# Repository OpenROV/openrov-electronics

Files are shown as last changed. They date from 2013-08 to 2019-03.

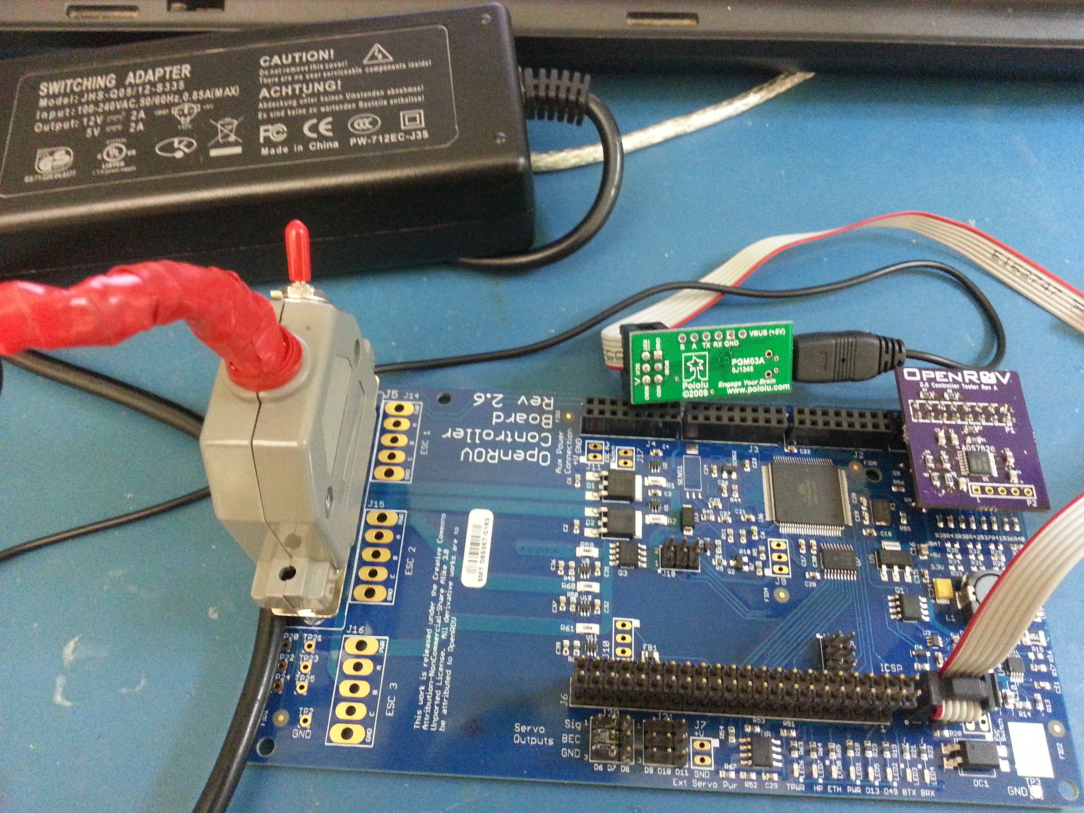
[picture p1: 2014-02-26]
OpenROV Controller Tester 2.6A/TestJig_Setup.jpg

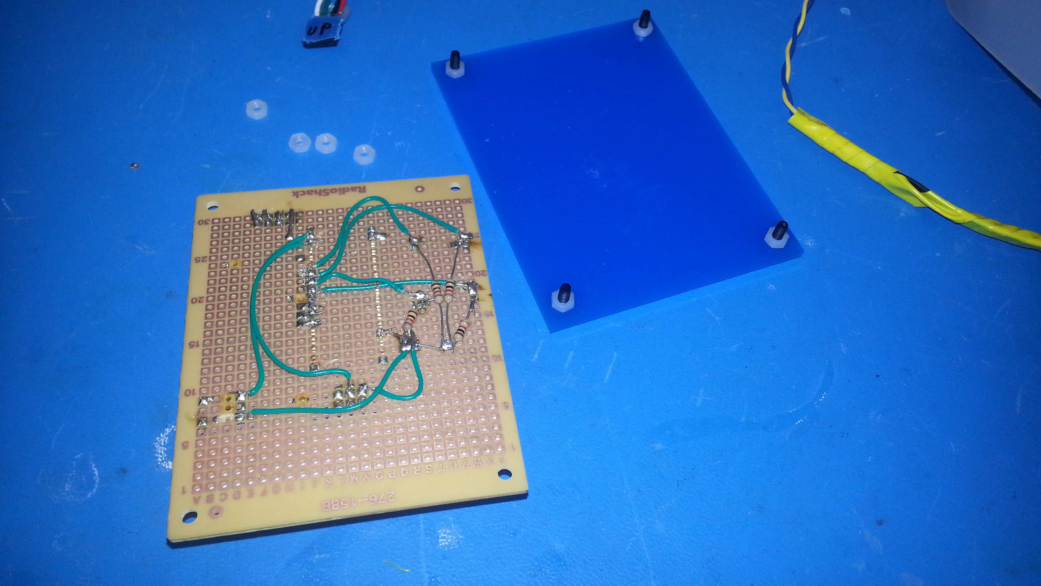
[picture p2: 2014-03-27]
OpenROV IMU Tester/backside2.jpg

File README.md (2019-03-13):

OpenROV
================
[OpenROV](http://openrov.com/) is a DIY telerobotics community centered around underwater exploration & adventure. Our [forum](https://forum.openrov.com/) is the primary place for community interaction and we encourage you to join us there!

Introduction
-------
This repository contains the electronics files for the OpenROV DIY Kits. These include the schematics, gerbers and the other files + diagrams.

Resources
-------
[Bill of Materials](https://docs.google.com/spreadsheet/ccc?key=0Avf6fUwp9B3kdF9YQWxBTnZjZEVGZVQwY25EbnVyREE&usp=sharing)

[Mechanical files](https://github.com/OpenROV/openrov-hardware)

Notes
-------
For OpenROV v2.6, v2.7, v2.8 see the OpenROV Controller Board Files.
  >It is a all-in-one power and control board that has an Arduino based Atmega 2560 aboard. Tons of I/O, and is designed to fit the BeagleBone Black.

For OpenROV v2.5 See the OpenROV Controller 2.5B. 
  >It is a all-in-one power and control board that has an Arduino based Atmega 2560 aboard. Tons of I/O, and is designed to fit both the BeagleBone Black and the original BeagleBone

For OpenROV V2.3 and V2.4, see the BeagleBone Cape A1. 
  >It is a all-in one power and control board based around the Atmega 328.

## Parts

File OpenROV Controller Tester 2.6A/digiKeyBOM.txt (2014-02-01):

Index,Quantity,Part Number,Description,Customer Reference,Available Quantity,Backorder Quantity,Unit Price USD,Extended Price USD,
1,3,296-12402-1-ND,IC ADC 12BIT 50KSPS 8CH 16TSSOP,,3,0,8.94000,$26.82,
2,10,399-1170-1-ND,CAP CER 0.1UF 50V 10% X7R 0805,,10,0,0.04400,$0.44,
3,5,399-1284-1-ND,CAP CER 1UF 16V 10% X7R 0805,,5,0,0.12000,$0.60,
4,20,RMCF0805FT10K0CT-ND,RES 10K OHM 1/8W 1% 0805,,20,0,0.02900,$0.58,
5,10,RMCF0805FT20K0CT-ND,RES 20K OHM 1/8W 1% 0805,,10,0,0.02900,$0.29,
6,10,311-49.9KCRCT-ND,RES 49.9K OHM 1/8W 1% 0805 SMD,,10,0,0.01900,$0.19,
7,12,RMCF0805JT4K70CT-ND,RES 4.7K OHM 1/8W 5% 0805,,12,0,0.02100,$0.25,
,,,,,,Subtotal,$29.17
,,,,,,Shipping,unknown
,,,,,,Estimated Sales Tax,$2.63
,,,,,,Total,unknown

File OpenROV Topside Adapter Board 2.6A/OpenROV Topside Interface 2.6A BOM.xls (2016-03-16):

 |  |  |  | OpenROV Topside Adapter 2.6A BOM - 11 Feb 2014
Parts | Qty | DNP? | OK to sub Sonic part? | Digi-Key Part# | Value | Device | Package | Description
C1, C2 | 2 |  | X | 1276-1082-1-ND | 10 uF X7R 16V | CAP1206 | R1206 | Generic Non-Polarized Capacitor
FB1 | 1 |  |  | 240-2551-1-ND | MI0805J102R-10 | FERRITESIZE_0805 | R0805 | Generic Surface Mount Ferrite Chip
FID1, FID2 | 2 | X |  |  | FIDUCIAL_1 | FIDUCIAL_1 | FIDUCIAL_1 | Alignment Fiducial
J1 | 1 |  | X | 609-4701-1-ND | FCI 10033526-N3212MLF | USB_MINI-BSURFACE_MOUNT | USB_MINI-B_SM | MINI USB-B Conector
J2 | 1 |  |  | 609-4537-ND | FCI 20020303-D021 | FCI_TERMINAL_BLOCK_2PL | FCI_09-381_2PL | FCI 2-place Terminal Block 09-381 / 20020303
J3, J4 | 2 |  | X | S2211EC-03-ND | Sullins PRPC003DFAN-RC | Header Pins 2x3 | SSW-103-02-S-D | 2X3 THROUGH-HOLE .025" SQ PINS w/ 0.32" Engagement Length
J5 | 1 | X |  |  |  | HDR_1X2X0.100-ALT_SILK | 22-23-2021_ALT_SILK | .100" (2.54mm) Center Header - 2 Pin
LED1 | 1 |  |  | 475-1404-1-ND | GREEN | LED-0805_BOTTOM_MT | LED_0805_BOTTOM_MT(OSRAM) | Generic LED
LED2, LED3 | 2 |  |  | 475-2553-1-ND | YELLOW | LED-0805_BOTTOM_MT | LED_0805_BOTTOM_MT(OSRAM) | Generic LED
R1 | 1 |  | X |  | 1K | RESISTOR-0805 | R0805 | Generic Resistor
R2, R6 | 2 |  | X |  | 0 (Jumper) | RESISTOR-0805 | R0805 | Generic Resistor
R3, R4 | 2 |  | X |  | 120 | RESISTOR-0805 | R0805 | Generic Resistor
R5 | 1 |  | X |  | 330 | RESISTOR-0805 | R0805 | Generic Resistor
U1 | 1 |  |  | AP1117IE33G-13DICT-ND | AP1117IE33G | AP1117SOT223 | SOT223 | Diodes, Inc. Voltage Regulator

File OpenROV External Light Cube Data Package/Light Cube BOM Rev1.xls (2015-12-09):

 |  |  |  | OpenROV Light Cube BOM - Revision 1 --- 8 Oct 2015
Qty | DNP? | OK to sub Sonic Part? | Digi-Key Part # | Value | Device | Package | Parts | Description
1 |  | X |  | 10 uF X6S 35V | CAP0805 | R0805 | C1 | Generic Non-Polarized Capacitor
1 |  | X |  | 1.0uF X7R 16V | CAP0603 | R0603 | C2 | Generic Non-Polarized Capacitor
2 |  |  | 568-4128-1-ND | PMEG3015EJ | SCHOTTKYSOD323 | SOD323 | D1, D3 | Silicon Schottky Diodes
1 |  |  | LM4040DIX3-2.5+TCT-ND | LM4040DIX3-2.5 | ZENER-TVS-SC70-3 | SC70-3 | D2 | Generic Zener Diode, TVS, or Reference Diode
1 |  |  | 240-2558-1-ND | MI0603L221R-10 | FERRITESIZE_0603 | R0603 | FB1 | Generic Surface Mount Ferrite Chip
1 | DNP |  |  |  | SMD_PAD3/3 | SMD_3_3 | GND | SMD PAD
1 |  |  | 240-2743-1-ND | 33 uH | INDUCTOR-LAIRD_TYS6045 | INDUCTOR_LAIRD_TYS6045 | L1 | Generic Inductor Footprint
1 |  |  | Mouser 941-XHP50A10D0BJ20E5 | CREE XHP50 4000K 1040 lm | LED_WITH_HEATSINK-CREE_XHP50_6V | CREE_XHP50_6V | LED1 | Power LED packages with a heatsink pad
1 |  |  | SI2318CDS-T1-GE3CT-ND | Si2318CDS | NMOS-FETSOT23 | SOT23 | Q1 | Generic NMOS FET
1 |  |  | 541-4.99KYCT-ND | 4.99K 1% 1/8W | RESISTOR-0402 | R0402 | R1 | Generic Resistor
1 |  |  | 490-6992-1-ND | Murata PRF18BG471QB5RB | RESISTOR-0603 | R0603 | R2 | Generic Resistor
2 |  | X |  | 4.7K 1% | RESISTOR-0402 | R0402 | R3, R5 | Generic Resistor
1 |  |  | 408-1421-1-ND | 0.12 1% 1/5W or higher | RESISTOR-0603 | R0603 | R4 | Generic Resistor
1 |  |  | ILD 4001 E6327CT-ND | ILD4001 | ILD4001 | SC74_INFINEON | U1 | Infineon ILD4001 Buck LED Controller
1 | DNP |  |  |  | SMD_PAD-2/2 | SMD_2_2 | V+ | SMD PAD

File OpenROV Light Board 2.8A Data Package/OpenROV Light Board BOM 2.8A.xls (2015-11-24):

 |  |  | OpenROV Light Board 2.8A BOM - 23 November 2015
Qty | DNP? | OK to sub Sonic Part? | Digi-Key Part # | Value | Device | Package | Parts | Description
3 |  | X |  | 0.01 uF X7R 50V | CAP0603 | R0603 | C1, C2, C4 | Generic Non-Polarized Capacitor
1 |  | X |  | 1A 30V Schottky | SCHOTTKYDO214AC | DO214AC | D1 | Silicon Schottky Diodes
1 |  |  | 507-1817-1-ND | 80mA /200 mA 15V | POLYFUSE-0603 | R0603 | F1 | Polyfuse / PPTC
2 | DNP |  |  | FIDUCIAL_1 | FIDUCIAL_1 | FIDUCIAL_1 | FID1, FID2 | Alignment Fiducial
2 | DNP |  |  |  | SOLDER_PADS_3MM | SOLDER_PADS_3MM | J1, J2 | Custom 3mm solder pads for OROV light board
2 | DNP |  |  |  | SOLDER_PADS_3MM-SMALL_HOLE | SOLDER_PADS_3MM_SMALL_HOLE | J3, J4 | Custom 3mm solder pads for OROV light board
4 |  |  | 160-2093-1-ND | LTW-5630AZL35 | LTW-5630AZL | LITEON-5630 | LED1, LED2, LED3, LED4 | Lite-On 5x3 mm LTW-5630AZL White LED
3 |  | X |  | 4.99K 1% | RESISTOR-0603 | R0603 | R1, R2, R3 | Generic Resistor
1 | DNP |  |  | DNP | RESISTOR-1206 | R1206 | R4 | Generic Resistor
2 |  |  | AL5812MP-13DICT-ND | AL5812MP-13 | AL5812MP-13 | MSOP-8EP | U1, U2 | Diodes, Inc AL5812 LED Driver

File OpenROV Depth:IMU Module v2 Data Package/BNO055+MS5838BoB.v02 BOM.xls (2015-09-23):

 |  |  | OpenROV Depth/IMU V2 BOM - 20 May 2015
Qty | DNP? | OK to sub Sonic part? | Part # | Value | Device | Package | Parts | Description
3 |  | X |  | 100 nF X5R 6.3V or greater | C-EUC0402 | C0402 | C1, C2, C3 | CAPACITOR, European symbol
1 |  | X |  | 6800 pF X7R 6.3V or greater | C-EUC0402 | C0402 | C4 | CAPACITOR, European symbol
1 |  | X |  | 4.7 uF X5R 6.3V or greater | C-EUC0402 | C0402 | C5 | CAPACITOR, European symbol
1 |  | X |  | 0.12 uF X5R 6.3V or greater | C-EUC0402 | C0402 | C6 | CAPACITOR, European symbol
2 | DNP |  |  | FIDUCIALUFIDUCIAL | FIDUCIALUFIDUCIAL | MICRO-FIDUCIAL | FID1, FID2 | Fiducial Alignment Points
2 | DNP |  |  | M021X02_NO_SILK | M021X02_NO_SILK | 1X02_NO_SILK | JP2, JP3 | Standard 2-pin 0.1" header. Use with
4 |  | X |  | 4K7 | R-US_R0402 | R0402 | R1, R2, R3, R5 | RESISTOR, American symbol
1 |  |  | Mouser 262-BNO055 | Bosch BNO055 | BN055 | LGA28 | U1
1 |  |  | MS5837-30BA | MS5837-30BA | MS5837 | MS5837 | U2 | Measurement Specialties' MS5837 Depth Sensor

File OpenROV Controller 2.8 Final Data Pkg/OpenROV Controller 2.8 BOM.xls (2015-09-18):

 |  |  | OpenROV Controller 2.8 BOM - 27 May 2015
Qty | DNP? | OK to sub Sonic Part? | Digi-Key Part # | Value | Device | Package | Parts | Description
25 |  | X |  | 0.1 uF | CAP0603 | R0603 | C1, C2, C3, C4, C5, C6, C7, C12, C15, C17, C18, C21, C22, C23, C24, C25, C26, C27, C28, C29, C30, C31, C32, C33, C43 | Generic Non-Polarized Capacitor
2 |  | X |  | 3900 pF 25V NP0 | CAP0603 | R0603 | C10, C11 | Generic Non-Polarized Capacitor
2 |  | X |  | 22 uF 10V X5R | CAP0805 | R0805 | C13, C14 | Generic Non-Polarized Capacitor
2 |  | X |  | 12 pF | CAP0603 | R0603 | C19, C20 | Generic Non-Polarized Capacitor
1 |  |  | 493-2098-1-ND | 220 uF 10V | CAP-POLARIZED-NICHICON-8MM | NICHICON_8MM | C34 | Electrolytic or Tantalum Capacitor
9 |  | X |  | 1 uF 25V X7R | CAP0603 | R0603 | C36, C37, C38, C42, C44, C45, C46, C47, C48 | Generic Non-Polarized Capacitor
3 |  |  | 493-3958-1-ND | 220 uF 35V Low-Impedance | CAP-POLARIZED-NICHICON-10MM | NICHICON_10MM | C39, C40, C41 | Electrolytic or Tantalum Capacitor
4 |  | X |  | 10 uF 25V X5R | CAP0805 | R0805 | C8, C9, C16, C35 | Generic Non-Polarized Capacitor
2 |  |  | MBRD835LT4GOSCT-ND | MBRD835L | SCHOTTKYDPAK | DPAK | D1, D2 | Silicon Schottky Diodes
1 |  |  | SMAJ18ALFCT-ND | SMAJ18A | ZENER-TVSDO-214AC | DO214AC | D3 | Generic Zener Diode, TVS, or Reference Diode
2 |  |  | MM3Z16VST1GOSCT-ND | 16.18V 2% | ZENER-TVSSOD323 | SOD323 | D4, D5 | Generic Zener Diode, TVS, or Reference Diode
1 |  |  | SMAJ15ALFCT-ND | SMAJ15A | ZENER-TVSDO-214AC | DO214AC | D6 | Generic Zener Diode, TVS, or Reference Diode
4 |  |  | S1AFSCT-ND | S1A | DIODE | DO214AC | D7, D8, D9, D10 | Generic Diode Devices
1 |  |  | 507-1749-1-ND | 2.0A / 4.0A 24V | POLYFUSE-2920 | R2920 | F1 | Polyfuse / PPTC
1 |  |  | 240-2504-1-ND | HZ0805B272R-10 | FERRITESIZE_0805 | R0805 | FB1 | Generic Surface Mount Ferrite Chip
5 | DNP |  |  | FIDUCIAL_1 | FIDUCIAL_1 | FIDUCIAL_1 | FID1, FID2, FID3, FID4, FID5 | Alignment Fiducial
1 |  | X | S7111-ND | Sullins PPPC082LFBN-RC | HDR_SOCKET_2X8 | SSW-108-02-S-D | J1 | 2x8 THROUGH-HOLE .025" SQ POST SOCKET
1 |  | X | SAM1030-03-ND |  | HDR_PINS_2X3 | HDR_PINS_2X3 | J13 | 2x3 PIN HEADER
1 |  |  |  | AfroESC 12A-stuff per instructions | ESC_PADS-AFRO-12/20A-ESC1S | AFRO-ESC-12/20A-ESC1S | J14 | Solder Pads for Various ESC Types
1 |  |  |  | AfroESC 12A-stuff per instructions | ESC_PADS-AFRO-12/20A-ESC2S | AFRO-ESC-12/20A-ESC2S | J15 | Solder Pads for Various ESC Types
1 |  |  |  | AfroESC 12A-stuff per instructions | ESC_PADS-AFRO-12/20A-ESC3S | AFRO-ESC-12/20A-ESC3S | J16 | Solder Pads for Various ESC Types
2 |  | X | S2211EC-03-ND | Sullins PRPC003DFAN-RC | HDR_SOCKET_2X3 | SSW-103-02-S-D | J18, J19 | 2X3 THROUGH-HOLE .025" SQ POST SOCKET
3 | DNP |  |  | PPPC082LFBN-RC (Not populated) | HDR_SOCKET_2X8 | SSW-108-02-S-D | J2, J3, J4 | 2x8 THROUGH-HOLE .025" SQ POST SOCKET
2 |  | X |  | TSW-103-07-G-T | HDR_PINS_3X3 | HDR_PINS_3X3 | J20, J21 | 3x3 0.100 Header Pins
1 |  |  | 182-25ME-ND | Norcomp 182-025-113R531 | M25VP | M25VP | J5 | 25-pin Vertical Male D-SUB
1 |  | X | Samtec DW-23-11-G-D-630 | Samtec DW-23-11-G-D-630 | BEAGLEBONE_PIN_HEADER | TSW-123-02-S-D | J6 | 46-pin Header for BeagleBone
4 | DNP |  |  |  | HDR_1X2X0.100-ALT_SILK | 22-23-2021_ALT_SILK | J7, J11, J12, J17 | .100" (2.54mm) Center Header - 2 Pin
2 | DNP |  |  |  | HDR_1X3X0.100-ALT_SILK | 22-23-2031_ALT_SILK | J9, J10 | .100" (2.54mm) Center Header - 3 Pin
1 |  |  | SRR1260-150MCT-ND | 15 uH 4A | INDUCTOR-BOURNS-12X0 | INDUCTOR_BOURNS_12X0 | L1 | Generic Inductor Footprint
2 |  |  | 475-2709-1-ND | GREEN | LED-0603 | LED_CHIPLED_0603 | LED1, LED6 | Generic LED
2 |  |  | 475-2506-1-ND | RED | LED-0603 | LED_CHIPLED_0603 | LED2, LED5 | Generic LED
4 |  |  | 475-1196-1-ND | YELLOW | LED-0603 | LED_CHIPLED_0603 | LED3, LED4, LED7, LED8 | Generic LED
1 |  |  | 160-2035-1-ND | LTV-8141S | LTV-8141S | DIL4-SMD | OC1 | Lite-On Bidirectional-Input Optocoupler
1 |  |  | 425-2103-1-ND | PC3H411NIP0F | OPTOCOUPLER-TRANSISTOR-BIDIR-MINIFLAT-HALFPITCH | OPTOCOUPLER-MINIFLAT-HALFPITCH | OC2 | Optocoupler with Bidirectional Input and Phototransistor Output (no Base Lead)
1 |  |  | SI4485DY-T1-GE3CT-ND | SI4485 | PMOS-FET | SO8 | Q1 | Generic PMOS FET
1 |  |  | DMN65D8L-7DICT-ND | DMN65D8L | NMOS-FETSOT23 | SOT23 | Q2 | Generic NMOS FET
1 |  |  | SI4459ADY-T1-GE3CT-ND | SI4459ADY | PMOS-FET | SO8 | Q3 | Generic PMOS FET
4 |  |  | IRLML6346TRPBFCT-ND | IRLML6346TR | NMOS-FETSOT23 | SOT23 | Q4, Q5, Q6, Q7 | Generic NMOS FET
2 |  |  | FDV301NCT-ND | FDV301N | NMOS-FETSOT23 | SOT23 | Q8, Q9 | Generic NMOS FET
5 |  |  | MCS1632R005FERCT-ND | 0.005 1% | RESISTOR-1206 | R1206 | R1, R2, R59, R60, R61 | Generic Resistor
2 |  | X |  | 10.0K 1% | RESISTOR-0603 | R0603 | R11, R17 | Generic Resistor
1 |  |  | WSLB-.025CT-ND | 0.025 1% | RESISTOR-0805 | R0805 | R12 | Generic Resistor
2 |  | X |  | 100K | RESISTOR-0603 | R0603 | R13, R20 | Generic Resistor
1 |  | X |  | 13.0K 1% | RESISTOR-0603 | R0603 | R14 | Generic Resistor
1 |  | X |  | 45.3K 1% | RESISTOR-0603 | R0603 | R16 | Generic Resistor
1 |  | X |  | 470 | RESISTOR-0603 | R0603 | R21 | Generic Resistor
9 | DNP |  |  | DNP | RESISTOR-0805 | R0805 | R24, R25, R27, R29, R30, R31, R33, R34, R35 | Generic Resistor
8 |  | X |  | 0 (Jumper) | RESISTOR-0805 | R0805 | R26, R28, R32, R70, R71, R72, R73, R74 | Generic Resistor
1 |  | X |  | 18K | RESISTOR-0603 | R0603 | R3 | Generic Resistor
3 |  | X |  | 30.1K 1% | RESISTOR-0603 | R0603 | R4, R10, R76 | Generic Resistor
1 | DNP |  |  | DNP | RESISTOR-0603 | R0603 | R47 | Generic Resistor
1 |  | X |  | 0 (Jumper) | RESISTOR-0603 | R0603 | R48 | Generic Resistor
6 |  | X |  | 3.3K | RESISTOR-0603 | R0603 | R49, R50, R66, R67, R68, R69 | Generic Resistor
12 |  | X |  | 1K | RESISTOR-0603 | R0603 | R5, R8, R9, R18, R19, R22, R23, R36, R37, R38, R39, R46 | Generic Resistor
8 |  | X |  | 4.7K | RESISTOR-0603 | R0603 | R51, R52, R53, R54, R55, R56, R57, R58 | Generic Resistor
11 |  | X |  | 10K | RESISTOR-0603 | R0603 | R6, R7, R15, R40, R41, R42, R43, R44, R45, R62, R75 | Generic Resistor
2 |  | X |  | 120 | RESISTOR-0603 | R0603 | R63, R64 | Generic Resistor
1 |  | X |  | 330 | RESISTOR-0603 | R0603 | R65 | Generic Resistor
1 | DNP |  |  | HIH-5031 (Not populated) | HIH-5031 | HIH-5031 | SENS1 | Honeywell Humidity Sensor
1 |  |  | MCP9701AT-E/TTCT-ND | MCP9701A | MCP9701 | SOT23 | SENS2 | Microchip Temperature Sensor. "A" version has better accuracy
9 | DNP |  |  |  | TEST_PAD-1.0 | 2.0/1.0 | TP1, TP2, TP3, TP20, TP21, TP22, TP23, TP24, TP25 | THROUGH-HOLE PADS
6 |  |  | 296-27331-1-ND | INA199A2 | INA199 | SC70-6L | U1, U2, U3, U9, U10, U11
1 |  |  | TCR2EF33LM(CTCT-ND | TCR2EF33 | TCR2EF | SOT23-5L | U12 | Toshiba TCR2EF 200 mA LDO Regulator
1 |  |  | 1028-1002-1-ND | Richtek RT8250 | RICHTEK_82XX | SO8-THERMAL | U4 | Richtek 82XX-series synchronous buck converter in SO-8 package
1 |  |  | 296-35976-1-ND | TLV1117LV33DCY | AP1117SOT223 | SOT223 | U5 | Diodes, Inc. Voltage Regulator
1 |  |  | ATMEGA2560-16AURCT-ND | ATMEGA2560-16AU | SMARTPRJ_ATMEGA25602560-16AU | SMARTPRJ_TQFP100 | U6 | ATMEGA MICROCONTROLLER from Arduino Refernce Design
1 |  |  | 296-21527-1-ND | TXB0108SSOP-20 | TXB0108SSOP-20 | SSOP-20 | U7 | TI Bidirectional Level Translator
1 |  |  | CAT24C256WI-GT3OSCT-ND | CAT24C256WI-G | CAT24C256WI-G | SO8 | U8 | I2C EEPROM for BeagleBone Capes
1 |  |  | 887-1747-1-ND | 16 MHz w/ 12pF Load | CRYSTAL-5*3.2 | DISCRETE_2P-SMD-5X3.2 | X1 | Crystal

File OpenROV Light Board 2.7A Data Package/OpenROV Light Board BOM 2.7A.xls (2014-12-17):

 |  |  | OpenROV Light Board 2.7A BOM - 7 September 2014
Qty | DNP? | OK to sub Sonic Part? | Digi-Key Part # | Value | Device | Package | Parts | Description
3 |  | X |  | 0.01 uF X7R 50V | CAP0603 | R0603 | C1, C2, C4 | Generic Non-Polarized Capacitor
1 |  | X |  | 1A 30V Schottky | SCHOTTKYDO214AC | DO214AC | D1 | Silicon Schottky Diodes
1 |  |  | 507-1817-1-ND | 80mA /120 mA 15V | POLYFUSE-0603 | R0603 | F1 | Polyfuse / PPTC
2 | DNP |  |  | FIDUCIAL_1 | FIDUCIAL_1 | FIDUCIAL_1 | FID1, FID2 | Alignment Fiducial
2 | DNP |  |  |  | HDR_1X2X0.100-ALT_SILK | 22-23-2021_ALT_SILK | J1, J2 | .100" (2.54mm) Center Header - 2 Pin
2 | DNP |  |  |  | HDR_1X2X2MM | 87758-0216 | J3, J4 | Original Source: Eagle Lib con-molex/87758-0216
4 |  |  | 160-2093-1-ND | LTW-5630AZL35 | LTW-5630AZL | LITEON-5630 | LED1, LED2, LED3, LED4 | Lite-On 5x3 mm LTW-5630AZL White LED
3 |  | X |  | 4.99K 1% | RESISTOR-0603 | R0603 | R1, R2, R3 | Generic Resistor
1 | DNP |  |  | DNP | RESISTOR-1206 | R1206 | R4 | Generic Resistor
2 |  |  | AL5812MP-13DICT-ND | AL5812MP-13 | AL5812MP-13 | MSOP-8EP | U1, U2 | Diodes, Inc AL5812 LED Driver

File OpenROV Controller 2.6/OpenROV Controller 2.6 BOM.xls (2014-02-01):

 |  |  | OpenROV Controller 2.6 BOM -- 13 Nov 2013
Qty | DNP? | OK to sub Sonic Part | Digi-Key Part# | Value | Device | Package | Parts | Description
27 |  | X | 445-1314-1-ND | 0.1 uF 50V X7R | CAP0603 | R0603 | C1, C2, C3, C4, C5, C6, C7, C12, C15, C17, C18, C21, C22, C23, C24, C25, C26, C27, C28, C29, C30, C31, C32, C33, C36, C37, C38 | Generic Non-Polarized Capacitor
1 |  | X | 399-1083-1-ND | 1000 pF 50V X7R | CAP0603 | R0603 | C11 | Generic Non-Polarized Capacitor
3 |  | X | 445-7660-1-ND | 10 uF 10V X5R | CAP0805 | R0805 | C13, C14, C16 | Generic Non-Polarized Capacitor
2 |  | X | 445-1270-1-ND | 12 pF NPO | CAP0603 | R0603 | C19, C20 | Generic Non-Polarized Capacitor
1 |  | X | 399-5756-1-ND | 220 uF 6.3V | CAP-POLARIZED-B_CASE | KEMET_B-CAPACITOR | C34
1 | DNP |  |  | DNP | CAP0805 | R0805 | C35 | Generic Non-Polarized Capacitor
3 |  | X | 1276-2396-1-ND | 1 uF 50V X5R | CAP0805 | R0805 | C8, C9, C10 | Generic Non-Polarized Capacitor
2 |  |  | MBRD835LT4GOSCT-ND | MBRD835L | SCHOTTKYDPAK | DPAK | D1, D2 | Silicon Schottky Diodes
1 |  |  | SMAJ22ALFCT-ND | SMAJ22A | ZENER-TVSDO-214AC | DO214AC | D3 | Generic Zener Diode or TVS
2 |  |  | MM3Z16VST1GOSCT-ND | 16.18V 2% | ZENER-TVSSOD323 | SOD323 | D4, D5 | Generic Zener Diode or TVS
1 |  |  | 641-1101-1-ND | CDBA340 | SCHOTTKYDO214AC | DO214AC | D6 | Silicon Schottky Diodes
4 |  |  | S1AFSCT-ND | S1A | DIODE | DO214AC | D7, D8, D9, D10 | Generic Diode Devices
1 |  |  | F5632CT-ND | 1.95A / 1.1A | POLYFUSE-1812 | R1812 | F1 | Polyfuse / PPTC
1 |  |  | 240-2504-1-ND | HZ0805B272R-10 | FERRITESIZE_0805 | R0805 | FB1 | Generic Surface Mount Ferrite Chip
5 | DNP |  |  | FIDUCIAL_1 | FIDUCIAL_1 | FIDUCIAL_1 | FID1, FID2, FID3, FID4, FID5 | Alignment Fiducial
4 |  | X | S7111-ND | Sullins PPPC082LFBN-RC | HDR_SOCKET_2X8 | SSW-108-02-S-D | J1, J2, J3, J4 | 2x8 THROUGH-HOLE .025" SQ POST SOCKET
1 |  | X | SAM1030-03-ND | Samtec TSW-103-07-L-D | HDR_PINS_2X3 | HDR_PINS_2X3 | J13 | 2x3 PIN HEADER
3 | DNP |  |  |  | ESC_PADS-0.156_ALT | ESC-PADS-.156-ALT_SILK | J14, J15, J16 | Solder Pads for ESC
2 |  | X | SAM1208-03-ND | SSW-103-01-G-D | HDR_SOCKET_2X3 | SSW-103-02-S-D | J18, J19 | 2X3 THROUGH-HOLE .025" SQ POST SOCKET
2 |  | X |  | TSW-103-07-G-T | HDR_PINS_3X3 | HDR_PINS_3X3 | J20, J21 | 3x3 0.100 Header Pins
1 |  |  | 609-3993-ND | FCI 10090096-P254 | M25VP | M25VP | J5 | 25-pin Vertical Male D-SUB
1 |  | X | Samtec DW-23-11-G-D-630 | Samtec DW-23-11-G-D-630 | BEAGLEBONE_PIN_HEADER | TSW-123-02-S-D | J6 | 46-pin Header for BeagleBone
4 | DNP |  |  |  | HDR_1X2X0.100-ALT_SILK | 22-23-2021_ALT_SILK | J7, J11, J12, J17 | .100" (2.54mm) Center Header - 2 Pin
2 | DNP |  |  |  | HDR_1X3X0.100-ALT_SILK | 22-23-2031_ALT_SILK | J9, J10 | .100" (2.54mm) Center Header - 3 Pin
1 |  |  | Order from Coilcraft | MSS1048-153MLB | INDUCTOR-MSS1048 | MSS1048 | L1 | Coilcraft MSS1048-series inductors
2 |  |  | 475-2709-1-ND | GREEN | LED-0603 | LED_CHIPLED_0603 | LED1, LED6 | Generic LED
2 |  |  | 475-2506-1-ND | RED | LED-0603 | LED_CHIPLED_0603 | LED2, LED5 | Generic LED
4 |  |  | 475-1196-1-ND | YELLOW | LED-0603 | LED_CHIPLED_0603 | LED3, LED4, LED7, LED8 | Generic LED
1 |  |  | 160-2035-1-ND | LTV-8141S | LTV-8141S | DIL4-SMD | OC1 | Lite-On Bidirectional-Input Optocoupler
1 |  |  | SI4485DY-T1-GE3CT-ND | SI4485 | PMOS-FET | SO8 | Q1 | Generic PMOS FET
1 |  |  | DMN65D8L-7DICT-ND | DMN65D8L | NMOS-FETSOT23 | SOT23 | Q2 | Generic NMOS FET
1 |  |  | SI4425DDY-T1-GE3CT-ND | SI4425 | PMOS-FET | SO8 | Q3 | Generic PMOS FET
4 |  |  | IRLML6346TRPBFCT-ND | IRLML6346TR | NMOS-FETSOT23 | SOT23 | Q4, Q5, Q6, Q7 | Generic NMOS FET
2 |  |  | FDV301NCT-ND | FDV301N | NMOS-FETSOT23 | SOT23 | Q8, Q9 | Generic NMOS FET
5 |  |  | MCS1632R005FERCT-ND | 0.005 1% | RESISTOR-1206 | R1206 | R1, R2, R59, R60, R61 | Generic Resistor
1 |  | X | P30.1KHCT-ND | 30.1K 1% | RESISTOR-0603 | R0603 | R10 | Generic Resistor
2 |  | X | P10.0KHCT-ND | 10.0K 1% | RESISTOR-0603 | R0603 | R11, R17 | Generic Resistor
1 |  |  | WSLB-.025CT-ND | 0.025 1% | RESISTOR-0805 | R0805 | R12 | Generic Resistor
1 |  | X | P133KHCT-ND | 133K 1% | RESISTOR-0603 | R0603 | R14 | Generic Resistor
1 |  |  | P75NACT-ND | 0.075 1% | RESISTOR-1210 | R1210 | R15 | Generic Resistor
1 |  | X | P9.76KHCT-ND | 9.76K 1% | RESISTOR-0603 | R0603 | R16 | Generic Resistor
1 |  | X | P100KGCT-ND | 100K | RESISTOR-0603 | R0603 | R20 | Generic Resistor
1 |  | X | P470GCT-ND | 470 | RESISTOR-0603 | R0603 | R21 | Generic Resistor
11 | DNP |  |  | DNP | RESISTOR-0603 | R0603 | R24, R25, R27, R29, R30, R31, R32, R33, R34, R35, R47 | Generic Resistor
4 |  | X | P0.0GCT-ND | 0 (Jumper) | RESISTOR-0603 | R0603 | R26, R28, R48, R67 | Generic Resistor
1 |  | X | P18KGCT-ND | 18K | RESISTOR-0603 | R0603 | R3 | Generic Resistor
14 |  | X | P10KGCT-ND | 10K | RESISTOR-0603 | R0603 | R4, R6, R7, R13, R40, R41, R42, R43, R44, R45, R49, R50, R62, R66 | Generic Resistor
12 |  | X | P1.0KGCT-ND | 1K | RESISTOR-0603 | R0603 | R5, R8, R9, R18, R19, R22, R23, R36, R37, R38, R39, R46 | Generic Resistor
8 |  | X | P4.7KGCT-ND | 4.7K | RESISTOR-0603 | R0603 | R51, R52, R53, R54, R55, R56, R57, R58 | Generic Resistor
2 |  | X | P120GCT-ND | 120 | RESISTOR-0603 | R0603 | R63, R64 | Generic Resistor
1 |  | X | P330GCT-ND | 330 | RESISTOR-0603 | R0603 | R65 | Generic Resistor
1 | DNP |  |  | HIH-5031 | HIH-5031 | HIH-5031 | SENS1 | Honeywell Humidity Sensor
1 |  |  | MCP9701AT-E/TTCT-ND | MCP9701A | MCP9701 | SOT23 | SENS2 | Microchip Temperature Sensor. "A" version has better accuracy
8 | DNP |  |  |  | TEST_PAD-1.0 | 2.0/1.0 | TP2, TP3, TP20, TP21, TP22, TP23, TP24, TP25 | THROUGH-HOLE PADS
6 |  |  | 296-27331-1-ND | INA199A2 | INA199 | SC70-6L | U1, U2, U3, U9, U10, U11
1 |  |  | LM25011MY/NOPBCT-ND | LM25011 | LM25011 | VSSOP-10 | U4 | TI LM25011 Switching Converter
1 |  |  | 296-35976-1-ND | TLV1117LV33 | AP1117SOT223 | SOT223 | U5 | Diodes, Inc. Voltage Regulator
1 |  |  | ATMEGA2560-16AURCT-ND | ATMEGA2560-16AU | SMARTPRJ_ATMEGA25602560-16AU | SMARTPRJ_TQFP100 | U6 | ATMEGA MICROCONTROLLER from Arduino Refernce Design
1 |  |  | 296-21527-1-ND | TXB0108SSOP-20 | TXB0108SSOP-20 | SSOP-20 | U7 | TI Bidirectional Level Translator
1 |  |  | CAT24C256WI-GT3OSCT-ND | CAT24C256WI-G | CAT24C256WI-G | SO8 | U8 | I2C EEPROM for BeagleBone Capes
1 |  |  | 887-1747-1-ND | 16 MHz w/ 12 pF load | CRYSTAL-5*3.2 | DISCRETE_2P-SMD-5X3.2 | X1 | Crystal

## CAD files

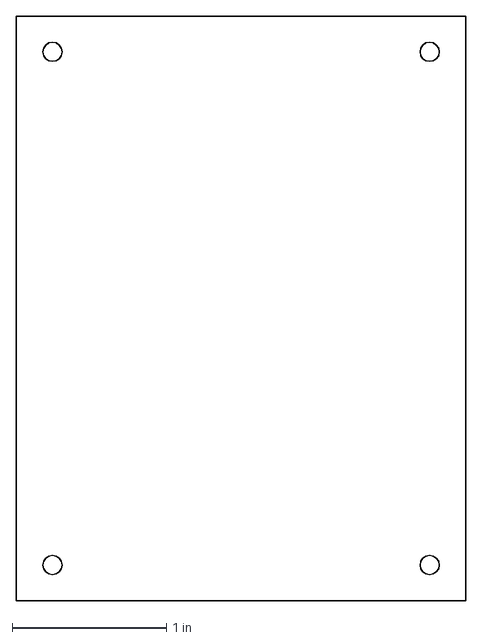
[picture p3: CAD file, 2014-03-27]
OpenROV IMU Tester/IMUTesterBottom.dxf
2.91 x 3.79 in

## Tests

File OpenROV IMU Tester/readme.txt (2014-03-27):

OpenROV IMU tester by Matthew Valancy! 

Basic bare IMU board test

1) Plug in the tester to USB power.
2) Connect IMU by tilting board on the header
3) Press soft reset button (the black one) 
4) Look at lights to see if IMU is OK
5) If IMU light is red then switch the address switch on the bottom of the tester and it will retest

Testing on ROV
Same as above but use Brians cable (DB25 to 4 pin IMU header)

Want to build another one because the original got destroyed or lost?

You need 4 LEDS, 1 toggle switch, 1 push button switch, 1 arduino. 
Wire with LEDS connected to ground through 1k resistor with positive side on arduino.
Toggle switch and push button are pulled high by arduino and set low when active.
Pins are shown in the arduino code.

Good luck.

Need help? scubasonar@gmail.com

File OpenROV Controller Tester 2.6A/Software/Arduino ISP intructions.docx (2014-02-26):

30 Oct 2013 W. Holm

Instructions for using the Pololu AVR ISP programmer with the Arduino IDE to program the OpenROV 2.5 boards

1.) Go to the Pololu web site, download the drivers for the programmer, and install them on your computer.

2.) Download the Arduino IDE and install. I'm using version 1.0.5.

3. Go to the directory C:\Program Files (x86)\Arduino\hardware\arduino

4.) Append the following text to the bottom of the programmers.txt file:

avrispv2.name=Pololu USB (AVRISPv2)

avrispv2.communication=serial

avrispv2.protocol=avrispv2

5.) Append the following text to the bottom of the boards.txt file:

mega2560p.name=Arduino Mega 2560 with Pololu AVR ISP

#mega2560p.upload.protocol=wiring

mega2560p.upload.using=avrispv2

mega2560p.upload.maximum_size=258048

#mega2560p.upload.speed=115200

mega2560.bootloader.low_fuses=0xFF

mega2560.bootloader.high_fuses=0xD8

mega2560.bootloader.extended_fuses=0xFD

mega2560.bootloader.path=stk500v2

mega2560.bootloader.file=stk500boot_v2_mega2560.hex

mega2560.bootloader.unlock_bits=0x3F

mega2560.bootloader.lock_bits=0x0F

mega2560p.build.mcu=atmega2560

mega2560p.build.f_cpu=16000000L

mega2560p.build.core=arduino

mega2560p.build.variant=mega

6.) Plug in the Pololu programmer to your computer.

7.) Probe what serial port is assigned to the programmer

8.) Open the Arduino IDE.

9.) In Tools/Boards, select "Arduino Mega 2560 with Pololu AVR ISP"

*we’ve been using Arduino Mega 2560 or Mega ADK

10.) In Tools/Programmer, select "Pololu USB"

11.) In Tools/Serial Port, select the serial port that the Pololu programmer is attached to.

12.) Apply power to the OROV controller board. The Pololu ISP cable does not apply power to the target.

13.) Attach the Pololu ISP cable to the ISP port on the board.

14.) Select Tools/Burn Bootloader and wait for the bootloader to be downloaded into the Controller board.

15.) Upload your desired sketch as you normally would in the Arduino IDE. Note that the serial monitor in the IDE will not work.

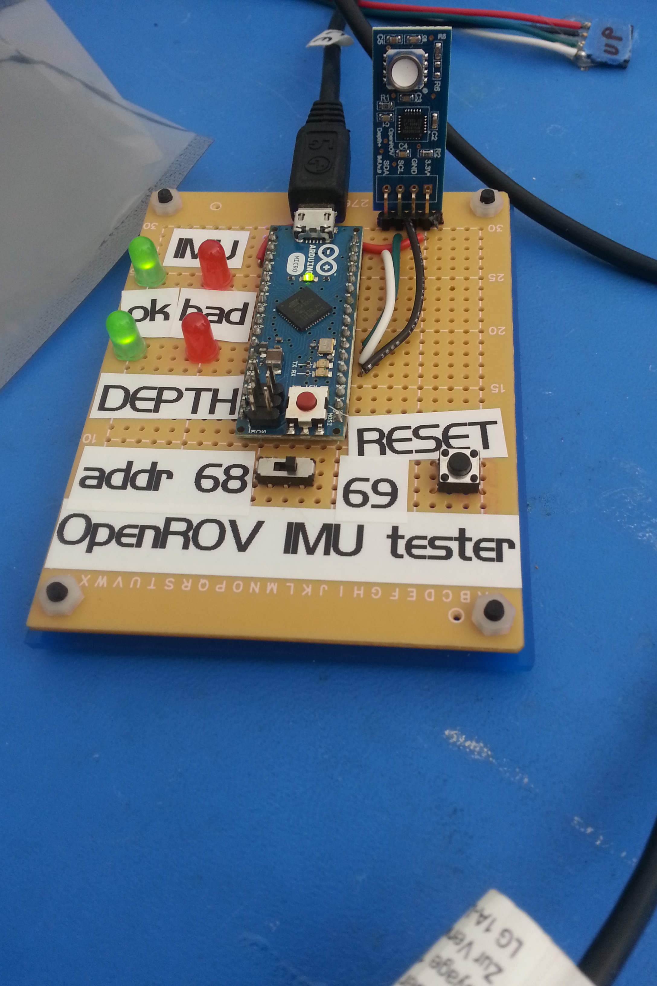
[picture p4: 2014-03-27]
OpenROV IMU Tester/front.jpg

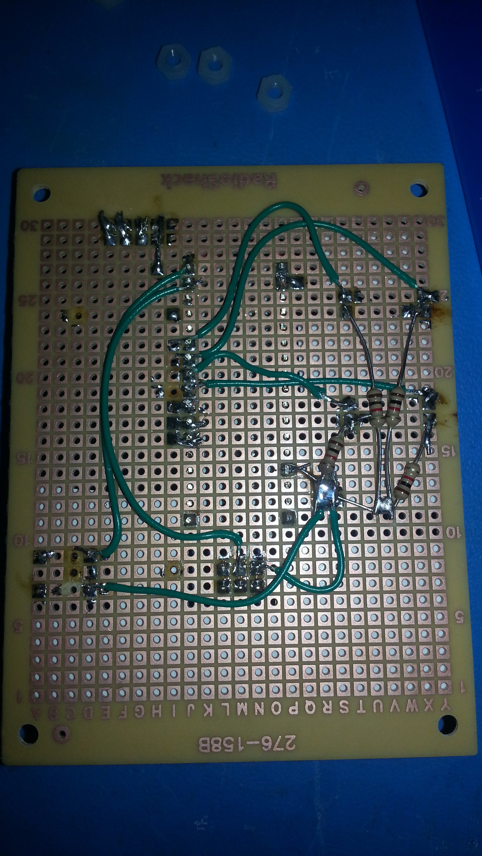
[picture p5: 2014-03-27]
OpenROV IMU Tester/backside.jpg

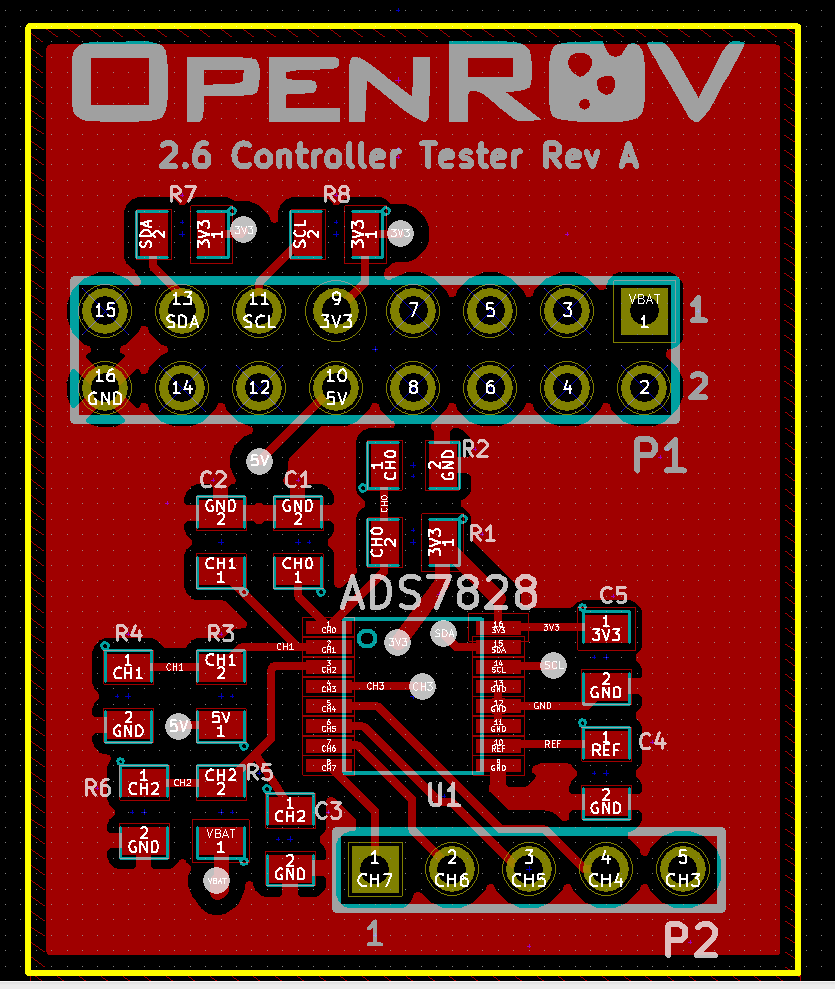
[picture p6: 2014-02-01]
OpenROV Controller Tester 2.6A/Controller Tester 2.6A Layout.png

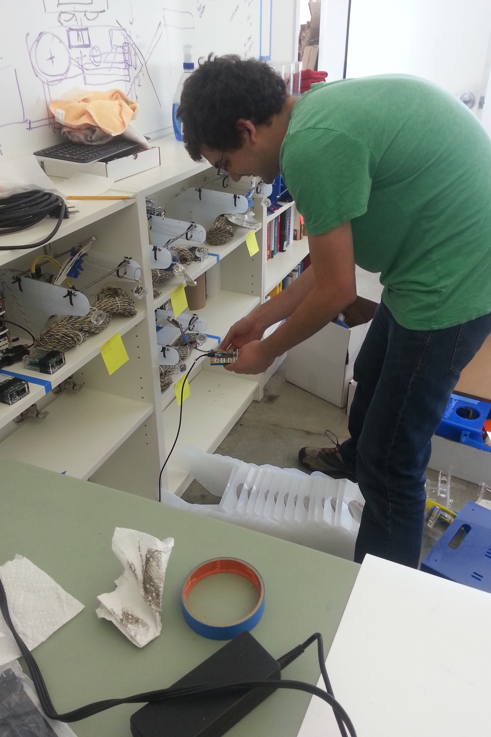
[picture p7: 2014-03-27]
OpenROV IMU Tester/inUse.jpg

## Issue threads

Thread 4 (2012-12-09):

No Clearance for Aux 2 Connector

davidtlang, 2012-12-09:
There isn't enough clearance for the Aux 2 connector because of the 5V barrel on the Beaglebone.

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

Closed 2015-01-07.

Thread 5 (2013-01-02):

Use Aux1 and Aux2 with other voltage sources

ThomasSo, 2013-01-02:
I could be a benefit for some users to change the power source for AUX1 & 2 from 12V_REG to V_BAT or other external power-source.
This is mostly for users that want to use higher than 12V to drive  equipment on AUX1 & 2
This also applies when the load on Aux exceeds the 1Amp spec. of the 12V regulator.

BrianAdams, 2015-01-07:
Done as of controllerboard 2.5

Closed 2015-01-07.

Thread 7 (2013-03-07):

Gold vs. Tin pins on servo header pins

WaltHolm, 2013-03-07:
The Cape that I purchased came pre-stuffed with tin-plated header pins on the servo headers (A-D, P6-P9 on the schematic).  Is this appropriate for the marine environment?  Will tin pins readily corrode when exposed to salt water? I'm wondering if we shouldn't switch to gold-plated pins for future production lots.

Closed 2015-01-07.

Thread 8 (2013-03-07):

Expand I2C Header (P4) on Cape

WaltHolm, 2013-03-07:
The current cape design has pads for a header (P4) to carry I2C data and clock lines to an external device (compass, depth sensor, whatever).  Any device using this is going to need power and ground as well, so it will need a second wiring harness for this.  If there is enough room, it would be nice to also have power and ground on header P4 so that a single cable can be used between the Cape and the I2C sensors.

While looking at this, I noted that the P2 I2C bus uses pullups to +5V.  If space is available, it would be nice to have a resistor stuff option to run the bus at +3.3V instead.

Closed 2015-01-07.

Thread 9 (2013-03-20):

Servo jumper on Cape in place while ESCs are plugged in should not damage anything

estackpole, 2013-03-20:
The servo jumper is used to supply 5v from the Cape power supply to the servo outputs if no ESCs are plugged into the Cape (which would normally supply their own 5v to the bus).  Electronics (perhaps some diodes) should be used to protect Cape from damage if 5v from the ESCs is attached to the 5v "input" from the cape through the jumper.

Closed 2015-01-07.

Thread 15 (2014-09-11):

Arduino needs to be able to power cycle the I2C power line

BrianAdams, 2014-09-11:
There are conditions where I2c devices are known to get confused and not recover after holding the SDL line low.  In this case the only way to recover is to reboot the slave devices.  A FET or other control on the power regulator to the I2c bus should solve the issue as long as it can be controlled by the Arduino

WaltHolm, 2015-10-09:
The 2.8 controller board implements this feature

Closed 2015-10-09.

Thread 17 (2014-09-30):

Humidity sensor pads need to be fixed

BrianAdams, 2014-09-30:
The ground of the lug tab is shorting the V+ right now.  Need to disconnect it from ground.

Workaround: Use an exacto knife to cut the trace that comes off of the pad so that the sensor is held mechanically but no longer connected to ground.

WaltHolm, 2015-10-09:
Fixed in Controller Board 2.8

Closed 2015-10-09.

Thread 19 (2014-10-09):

Need a way to detect loss of power before the capacitors finish discharging

BrianAdams, 2014-10-09:
Assuming we get anywhere close to the 100ms of run time off of the capacitor, we need to be able to sense the power loss so that we can gracefully flush the disks to avoid disk corruption.

BrianAdams, 2015-03-13:
How big of a can of worms would it be to incorporate a backup battery on to the beaglebone so that we can always gracefully shutdown?

WaltHolm, 2015-10-09:
A feature was implemented in Controller Board 2.8 to signal the ATmega2560 (Arduino) processor ~100msec before power is shut down

Closed 2015-10-09.

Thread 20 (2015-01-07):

Add write mode pads to eeprom for controllerboard

BrianAdams, 2015-01-07:
Add pads to BB cape eeprom so that the bed of nails can disable write protect

WaltHolm, 2015-10-09:
Implemented on Controller Board 2.8

Closed 2015-10-09.

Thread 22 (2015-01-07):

Fix ramp of the 3.3V power supply

BrianAdams, 2015-01-07:
Change soft start capacitor C11 to smooth out the ramp of the 3.3V power supply.  It currently is out of spec.

WaltHolm, 2015-10-09:
Fixed in Controller Board 2.8

Closed 2015-10-09.

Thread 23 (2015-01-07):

Enable external LED capability to the board

BrianAdams, 2015-01-07:
Add wiring from PWM3 to external TB20 and TB21 to support external LEDs
Stuff R32 to enable PWM3 from the factory

WaltHolm, 2015-10-10:
Done in Controller Board 2.8.   There are 0-ohm resistors in the PWM3 traces to TP20 and TP21, so that PWM3 can be disconnected from TP20 and TP21 if desired

Closed 2015-10-10.

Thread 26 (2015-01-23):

Move external power input to board periphery

BrianAdams, 2015-01-23:
The current connector pads for adding external power to the controller board are hard to access once the board is mounted in an ROV.  Find a way to move these pins to the periphery of the board so that it can be easily connectorized.

WaltHolm, 2015-10-10:
Done on Controller Board 2.8

Closed 2015-10-10.

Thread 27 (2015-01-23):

Improve filtering on current measurement telemetry points

BrianAdams, 2015-01-23:
Telemetry of the current measurements is very noisy due to undersampling.  Reduce the corner frequency of the filtering to smooth out this data.

BrianAdams, 2015-01-23:
Currently no filter on the Battery tubes
ESCs have .1uf and 10k ~150hz, Should slow the corner frequency to about 50hz to target a 100hz sample rate.

WaltHolm, 2015-10-10:
On Controller board 2.8, filtering was added on Battery Current measurement points.  Corner frequency on all current measuring points was lowered to 50 Hz.

Closed 2015-10-10.

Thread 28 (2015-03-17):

Explicitly declare every IO line so it is in a known state

BrianAdams, 2015-03-17:
All of the Arduino pins reset to tri-state. They should all be set to a known state be default.

BrianAdams, 2015-04-21:
Leaving open for Walt to include what needs to be include in the app note.

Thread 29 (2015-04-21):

2.7 part out of production: Voltage Regulator for I2C needs to be replaced

BrianAdams, 2015-04-21:

WaltHolm, 2015-10-10:
Part was retained in production - no change necessary

Closed 2015-10-10.

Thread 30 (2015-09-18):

Some 2.8 Controller boards failing QA at higher than desired rates on QA step 18

BrianAdams, 2015-09-18:
On step 18 is our burning the fuses on the mega2560. Debugging shows that the mega2560 is talking via the ISP communication, but that the attempt to put it in programming mode fails.

Good board
===
avrdude: Send: . [1b] . [0d] . [00] . [0c] . [0e] . [10] . [c8] d [64] . [19]   [20] . [00] S [53] . [03] . [ac] S [53] . [00] . [00] > [3e]
avrdude: Recv: . [1b]
avrdude: Recv: . [0d]
avrdude: Recv: . [00]
avrdude: Recv: . [02]
avrdude: Recv: . [0e]
avrdude: Recv: . [10]
avrdude: Recv: . [00] -> OK
avrdude: Recv: . [0a]
avrdude: AVR device initialized and ready to accept instructions

Bad Board
===
avrdude: Send: . [1b] . [0d] . [00] . [0c] . [0e] . [10] . [c8] d [64] . [19]   [20] . [00] S [53] . [03] . [ac] S [53] . [00] . [00] > [3e]
                Read Sig
                      Ret Addr
                                OK
                                      CMD1    CMD2
                                             CMD_ENTER_PROGMODE_ISP

avrdude: Recv: . [1b] -> Command
avrdude: Recv: . [0d] -> Matched previous sequence number/register
avrdude: Recv: . [00] -> OK
avrdude: Recv: . [02] -> Respon Body length
avrdude: Recv: . [0e] -> Begininig of response body
avrdude: Recv: . [10] -> CMD_ENTER_PROGMODE_ISP
avrdude: Recv: . [c0] -> STATUS_CMD_FAILED
avrdude: Recv: . [ca] -> Checksum
avrdude: stk500v2_command(): command failed
avrdude: initialization failed, rc=-1
         Double check connections and try again, or use -F to override
         this check.

WaltHolm, 2015-10-10:
The problem was isolated to a bad batch of ATMega2560s.  They are being swapped out at the assembly house.

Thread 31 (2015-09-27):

Increase Copper Cuttout Hole on 2.8 Light Board

briangrau, 2015-09-27:
The M2 screws that are used to secure the camera board in place also go through the camera board and can cause the grounds to connect causing the lights to always be on and no user control. This seems to happen when the screws are tightened down a lot and is cutting though the coating on the light board plate.

briangrau, 2015-09-28:
Here is the forum thread where this problem was first brought to our attention.

https://forum.openrov.com/t/led-lights-on-all-the-time/3276

WaltHolm, 2015-10-10:
The copper pour in the area of the screws needs to be opened up so that the screw head cannot touch the copper.

briangrau, 2015-11-24:
Fixed in Light Board 2.8A

https://github.com/OpenROV/openrov-electronics/commit/51dcb5fd4651239b08779614ee4c81552e01517a

Closed 2015-11-24.

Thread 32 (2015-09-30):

BBB does not always start

BrianAdams, 2015-09-30:
*Note this issue may move.  It needs confirmation on the state of the LEDS to confirm to confirm it is different than the UART issue that prevents boots*

There are a couple of scenarios that we have seen.

The issue
----

The power led comes on but other BBB activity is observed.  Pressing the reset button seems to fix the issue.  This is a major issue that we are seeing as recently as the 30.0.3 pre-release software builds.  This does not appear to be a software issue as the entire system seems to fail to start.  We recently attempted to power cycle [6 BBB 30 times](https://openrov.ontestpad.com/script/5#/1/).  We ended up with 8 failed boots, so a **4.5%** boot failure rate.  All boards were Element14 boards.

Other boot issues that are out of scope for this issue
----
The power + 2 BBB leds come on.  One LED seems to be a heart beat and the other one seems to constantly blink like its doing something but the board stays in that state.  We typically identify these as "corrupted disk images" which we are handling as a Software Issue.

There is another known issue that should be fixed via the latest UBOOT software.  There was an issue with junk on the UART pin stopping the boot process where you would get the power led + 1 other led in a steady state.  https://groups.google.com/d/msg/beagleboard/aXv6An1xfqI/-3ijviL1bzUJ

BrianAdams, 2015-10-02:
Interesting. According to RCN https://groups.google.com/d/msg/beagleboard/aXv6An1xfqI/67CHDM6rIQAJ the patched version of the uboot that helps protect from noise on the UART is only doing so by checking for *any* key to be pressed.  Apparently CircuitCo test machines need this.  Everyone else was patching with a key sequence.

So in theory, if the UART reads a value off the floating rx line that happens to be in a valid key range then the boot sequence would still stop.

BrianAdams, 2015-10-02:
We have confirmation that indeed, random noise on the UART line can still cause boot failures.  This is most likely what is happening. https://groups.google.com/d/msg/beagleboard/aXv6An1xfqI/wzdRNIIzCwAJ

There is a software only fix, we just have to figure out how to slip stream it in to the build process.

The software patch and hardware fix are both detailed here: http://www.mikini.dk/index.php/category/beaglebone-black/boot-issue

BrianAdams, 2015-10-02:
This is a link to a simplified version of the software patch: https://groups.google.com/d/msg/beagleboard/aXv6An1xfqI/T8Z8HqLFZYcJ

Closed 2015-10-08.

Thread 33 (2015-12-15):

Change LEDs on Topside Adapter

briangrau, 2015-12-15:
The LEDs that were being used are no longer being stocked. They were replaced with the following.

LUMEX SSL-LXA228GC-TR31
LUMEX SSL-LXA228YC-TR31

These LEDs are harder to come by, so future board designs should be designed to accept a different style of LED.

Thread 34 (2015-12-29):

Add Polyfuse Protection to Controller Board Tester

briangrau, 2015-12-29:
Add protection to the tester in case of problems with the controller boards.

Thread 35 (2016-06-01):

Topside interface board: Expose 5V power and GND as solder points

codewithpassion, 2016-06-01:
To power the topside interface board from other sources than the USB port (for example for the community hack http://openrov.dozuki.com/Guide/How+to+build+a+USB-Ethernet+topside+adapter/54), the 5V power and GND lines should be exposed via solder points. This way people don't have to solder onto existing pins.

This is probably a duplicate or replacement for #18.

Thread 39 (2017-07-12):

IMU

briangrau, 2017-07-12:
High tolerance holes or make them bigger for the 2 series to make sure that with hole tolerance the wires still fit in.

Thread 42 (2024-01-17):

Bill of Materials link is dead

EngineeringOV, 2024-01-17:
The google sheets link says

"
Sorry, the file you have requested has been deleted.

Make sure that you have the correct URL and the owner of the file hasn't deleted it.

Get stuff done with Google Drive

Apps in Google Drive make it easy to create, store and share online documents, spreadsheets, presentations and more.

Learn more at [drive.google.com/start/apps](https://drive.google.com/start/apps).
"

Does anybody have a copy of it?

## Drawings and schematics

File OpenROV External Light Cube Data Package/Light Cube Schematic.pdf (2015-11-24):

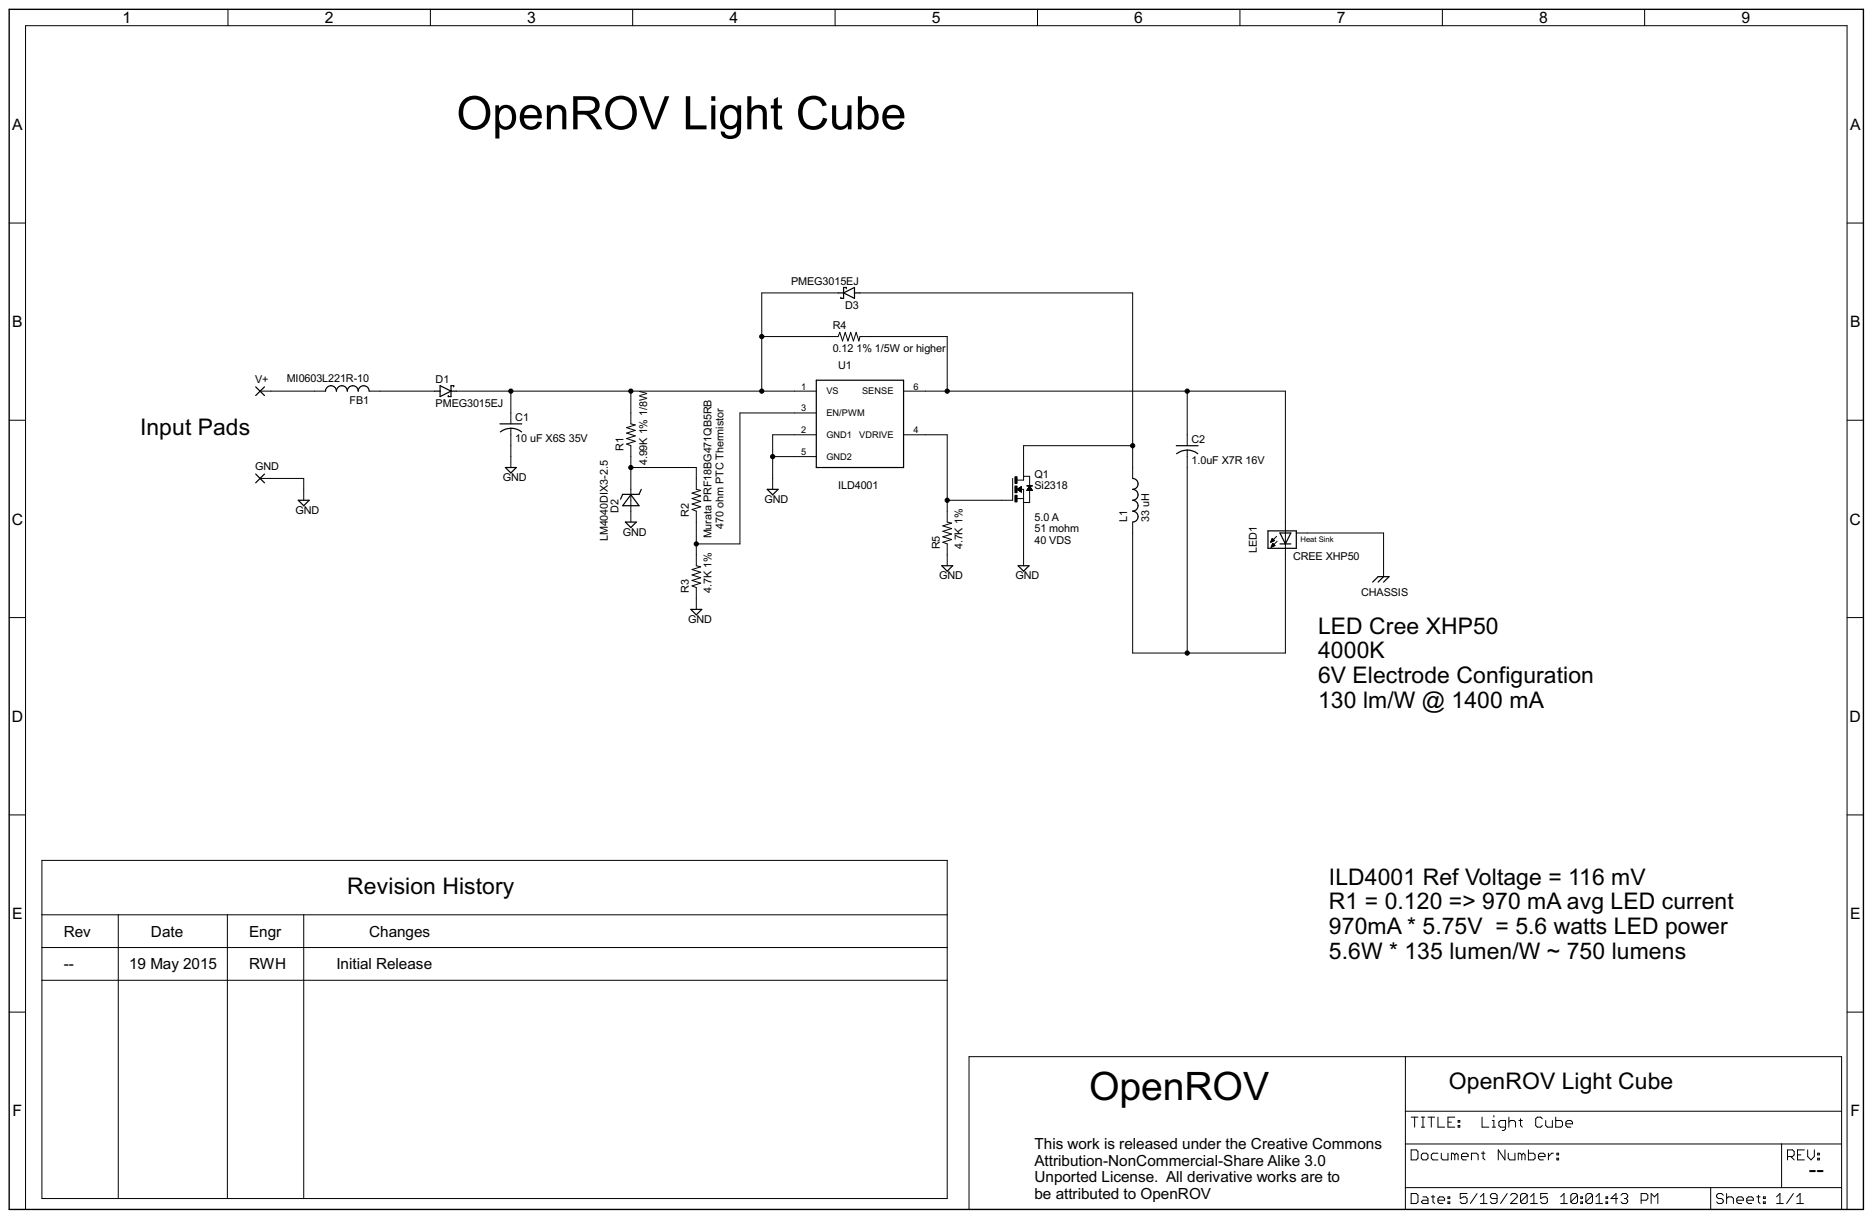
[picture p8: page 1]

ILD4001 Ref Voltage = 116 mV
R1 = 0.120 => 970 mA avg LED current
970mA * 5.75V = 5.6 watts LED power
5.6W * 135 lumen/W ~ 750 lumens

Rev | Date | Engr | Changes

-- | 19 May 2015 | RWH | Initial Release

be attributed to OpenROV OpenROV

This work is released under the Creative Commons Attribution-NonCommercial-Share Alike 3.0 Unported License. All derivative works are to

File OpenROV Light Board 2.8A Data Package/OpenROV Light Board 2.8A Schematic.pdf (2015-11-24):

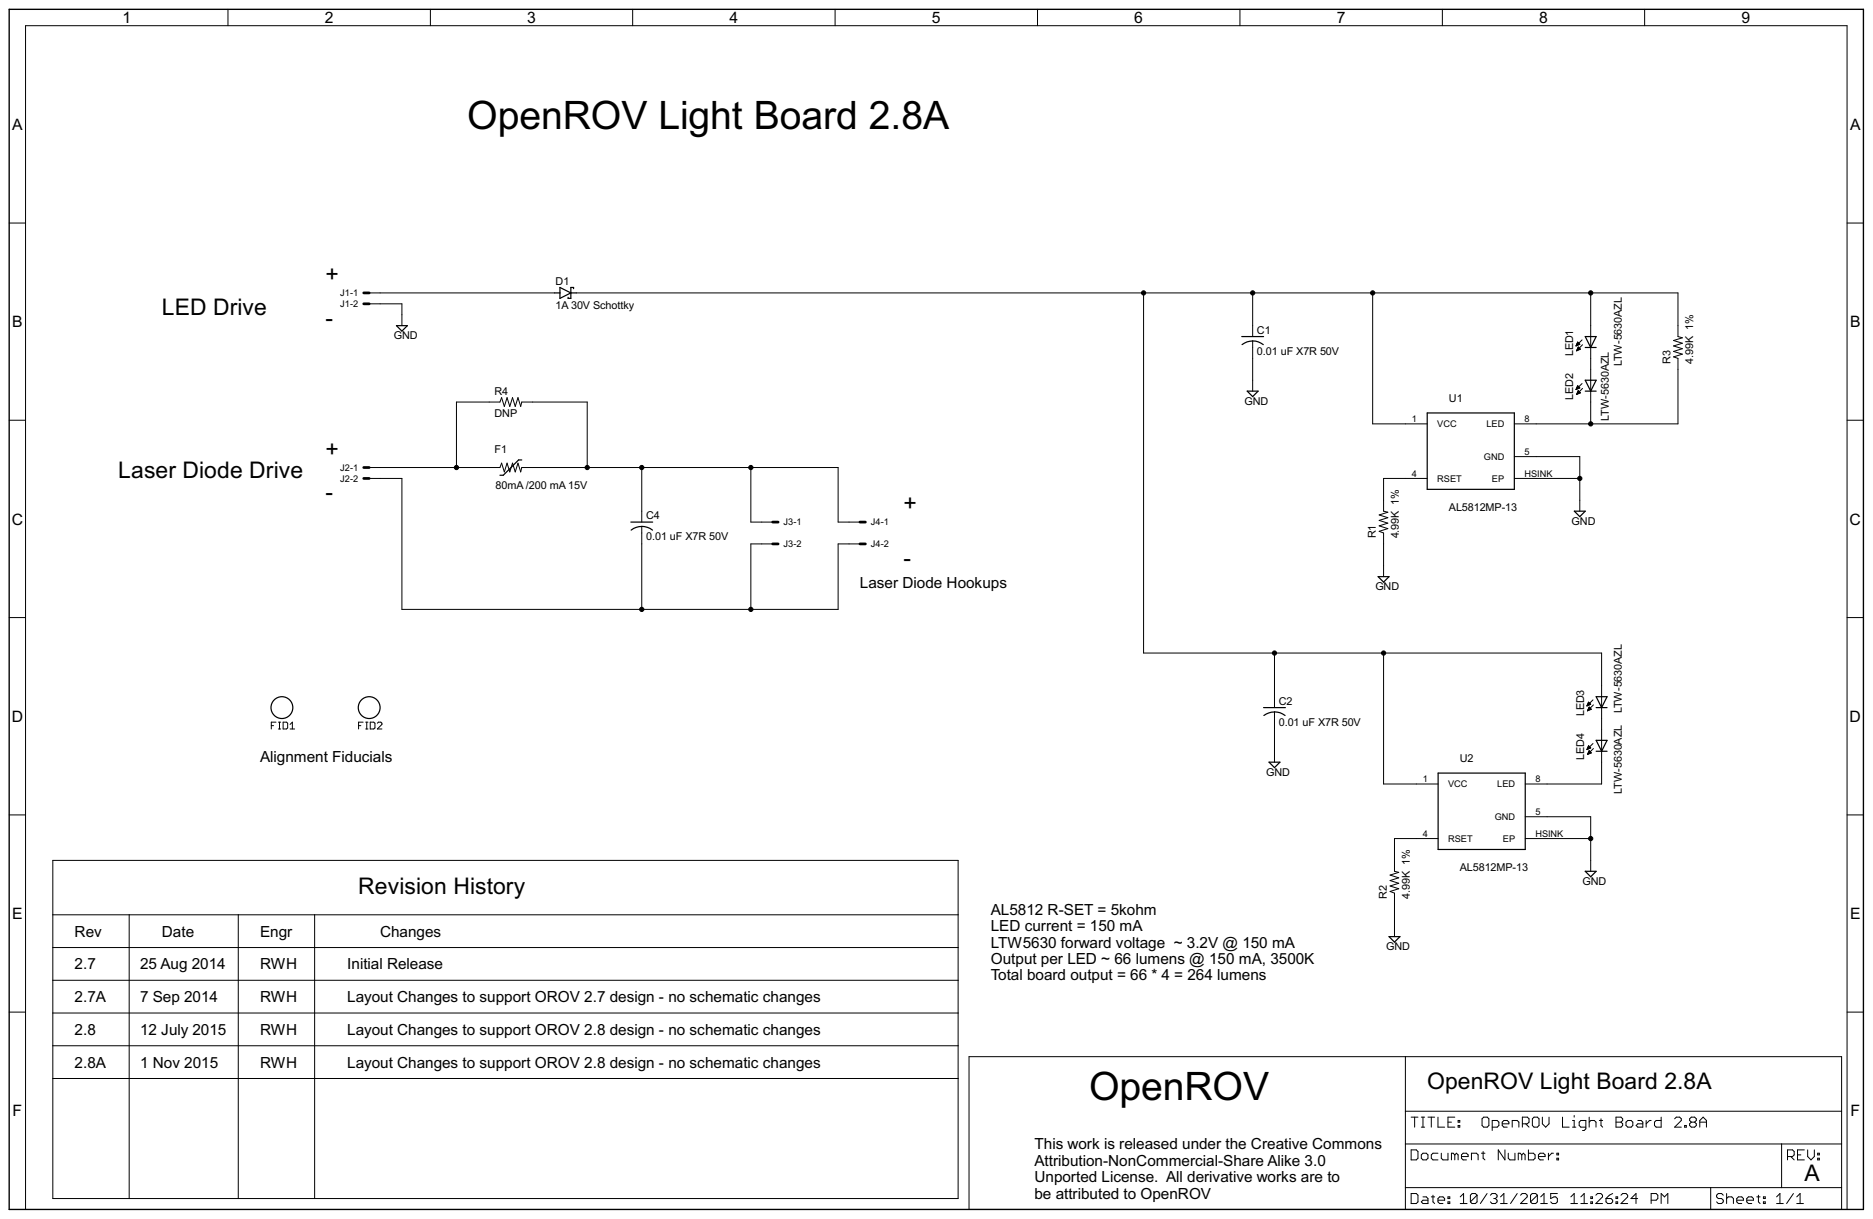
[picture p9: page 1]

AL5812 R-SET = 5kohm
LED current = 150 mA
LTW5630 forward voltage ~ 3.2V @ 150 mA Output per LED ~ 66 lumens @ 150 mA, 3500K

Rev | 25 Aug 2014 Date | Engr RWH | Initial Release Changes 2.7

2.7A | 1 Nov 2015 7 Sep 2014 12 July 2015 | RWH RWH RWH | Layout Changes to support OROV 2.8 design - no schematic changes Layout Changes to support OROV 2.7 design - no schematic changes 2.8 Layout Changes to support OROV 2.8 design - no schematic changes | Total board output = 66 * 4 = 264 lumens 2.8A

be attributed to OpenROV OpenROV

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

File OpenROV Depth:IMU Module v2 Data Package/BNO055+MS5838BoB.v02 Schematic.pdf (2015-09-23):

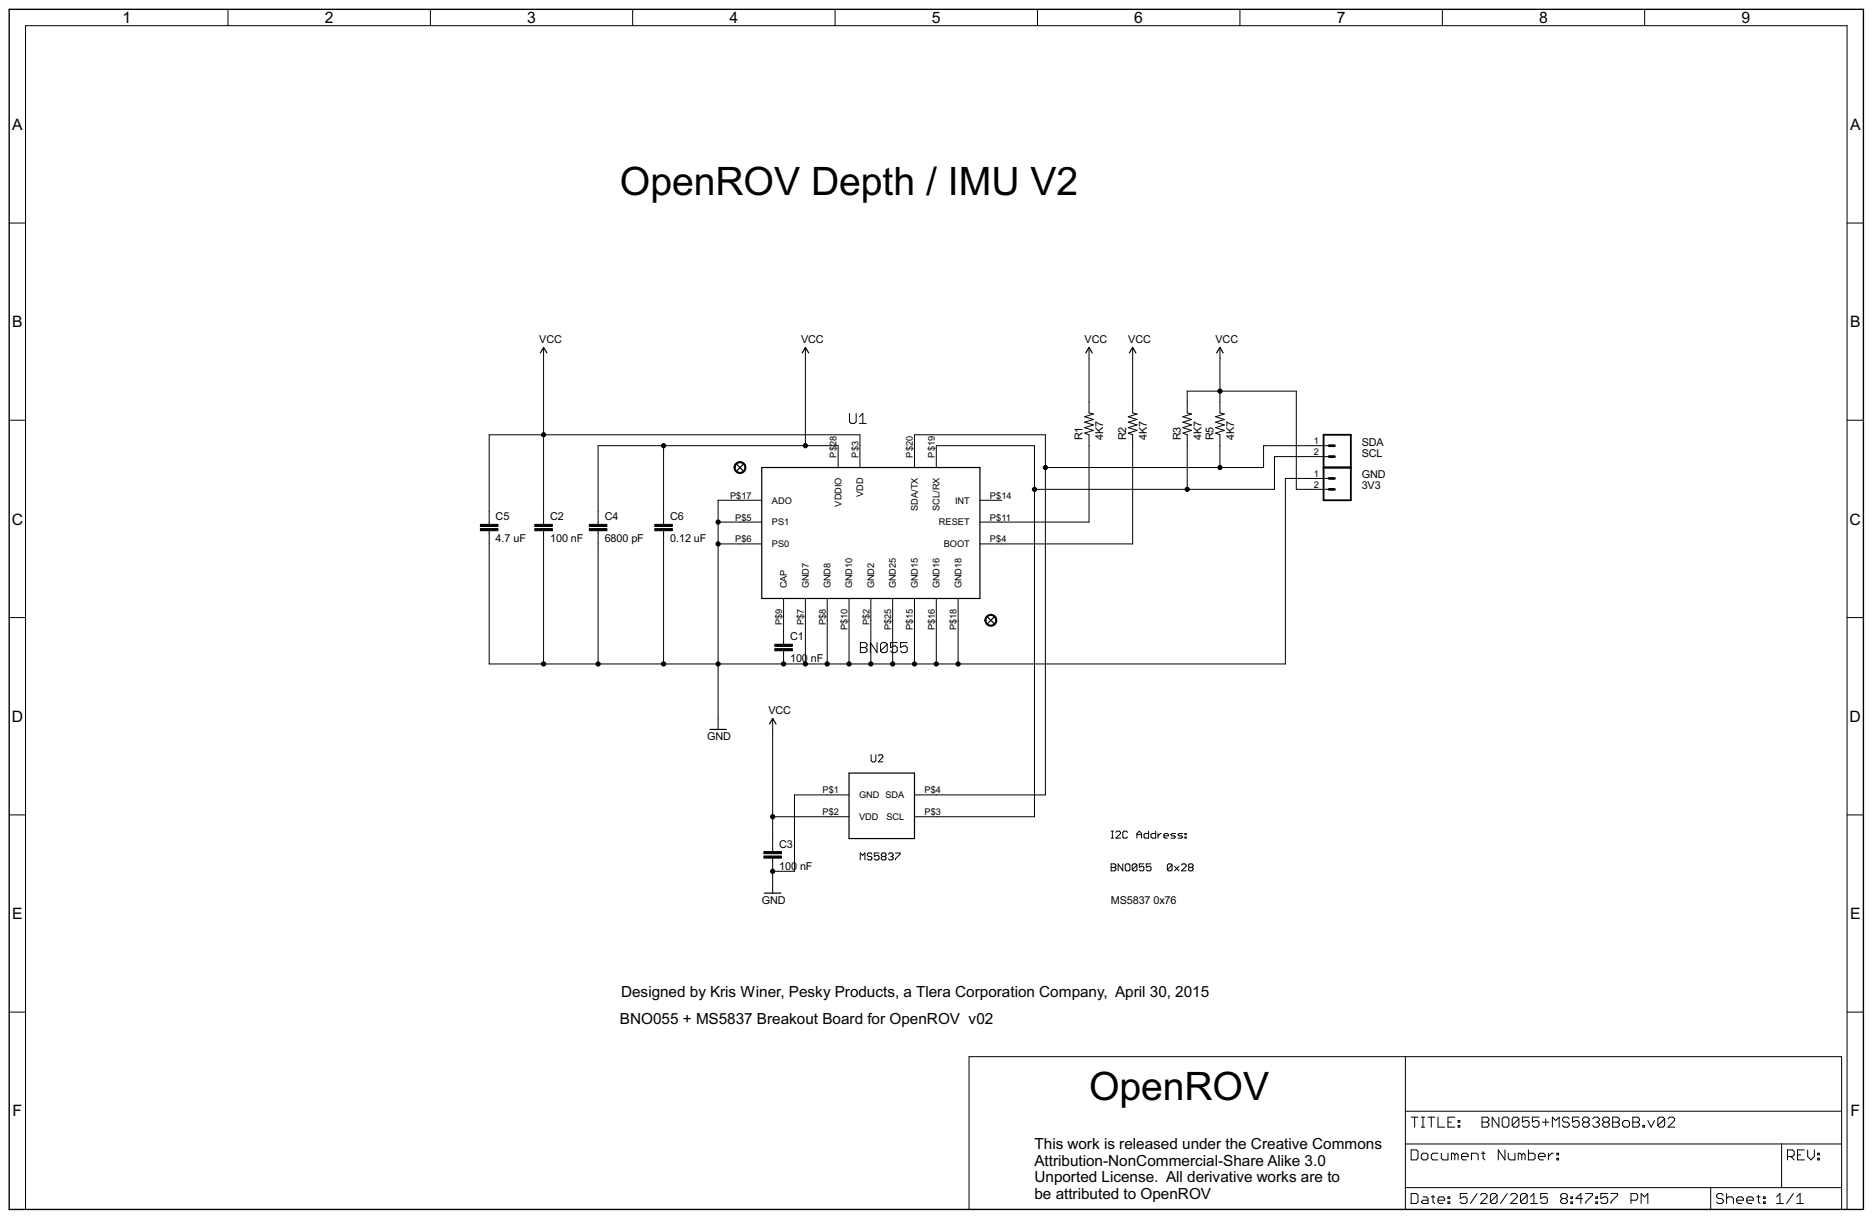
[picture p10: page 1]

Designed by Kris Winer, Pesky Products, a Tlera Corporation Company, April 30, 2015 BNO055 + MS5837 Breakout Board for OpenROV v02

be attributed to OpenROV OpenROV

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

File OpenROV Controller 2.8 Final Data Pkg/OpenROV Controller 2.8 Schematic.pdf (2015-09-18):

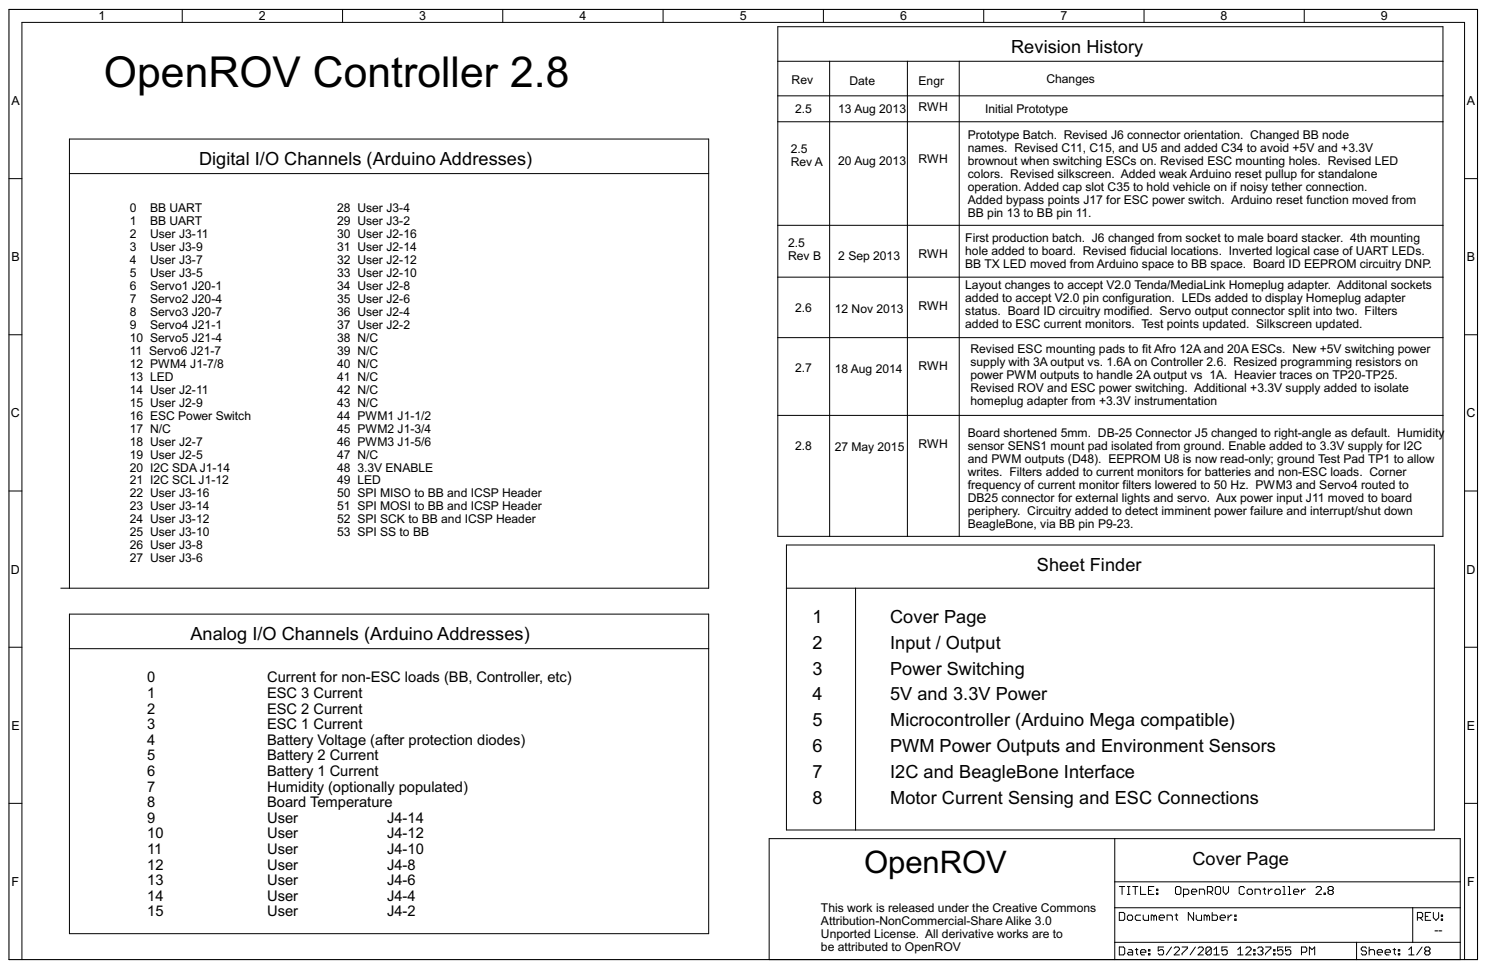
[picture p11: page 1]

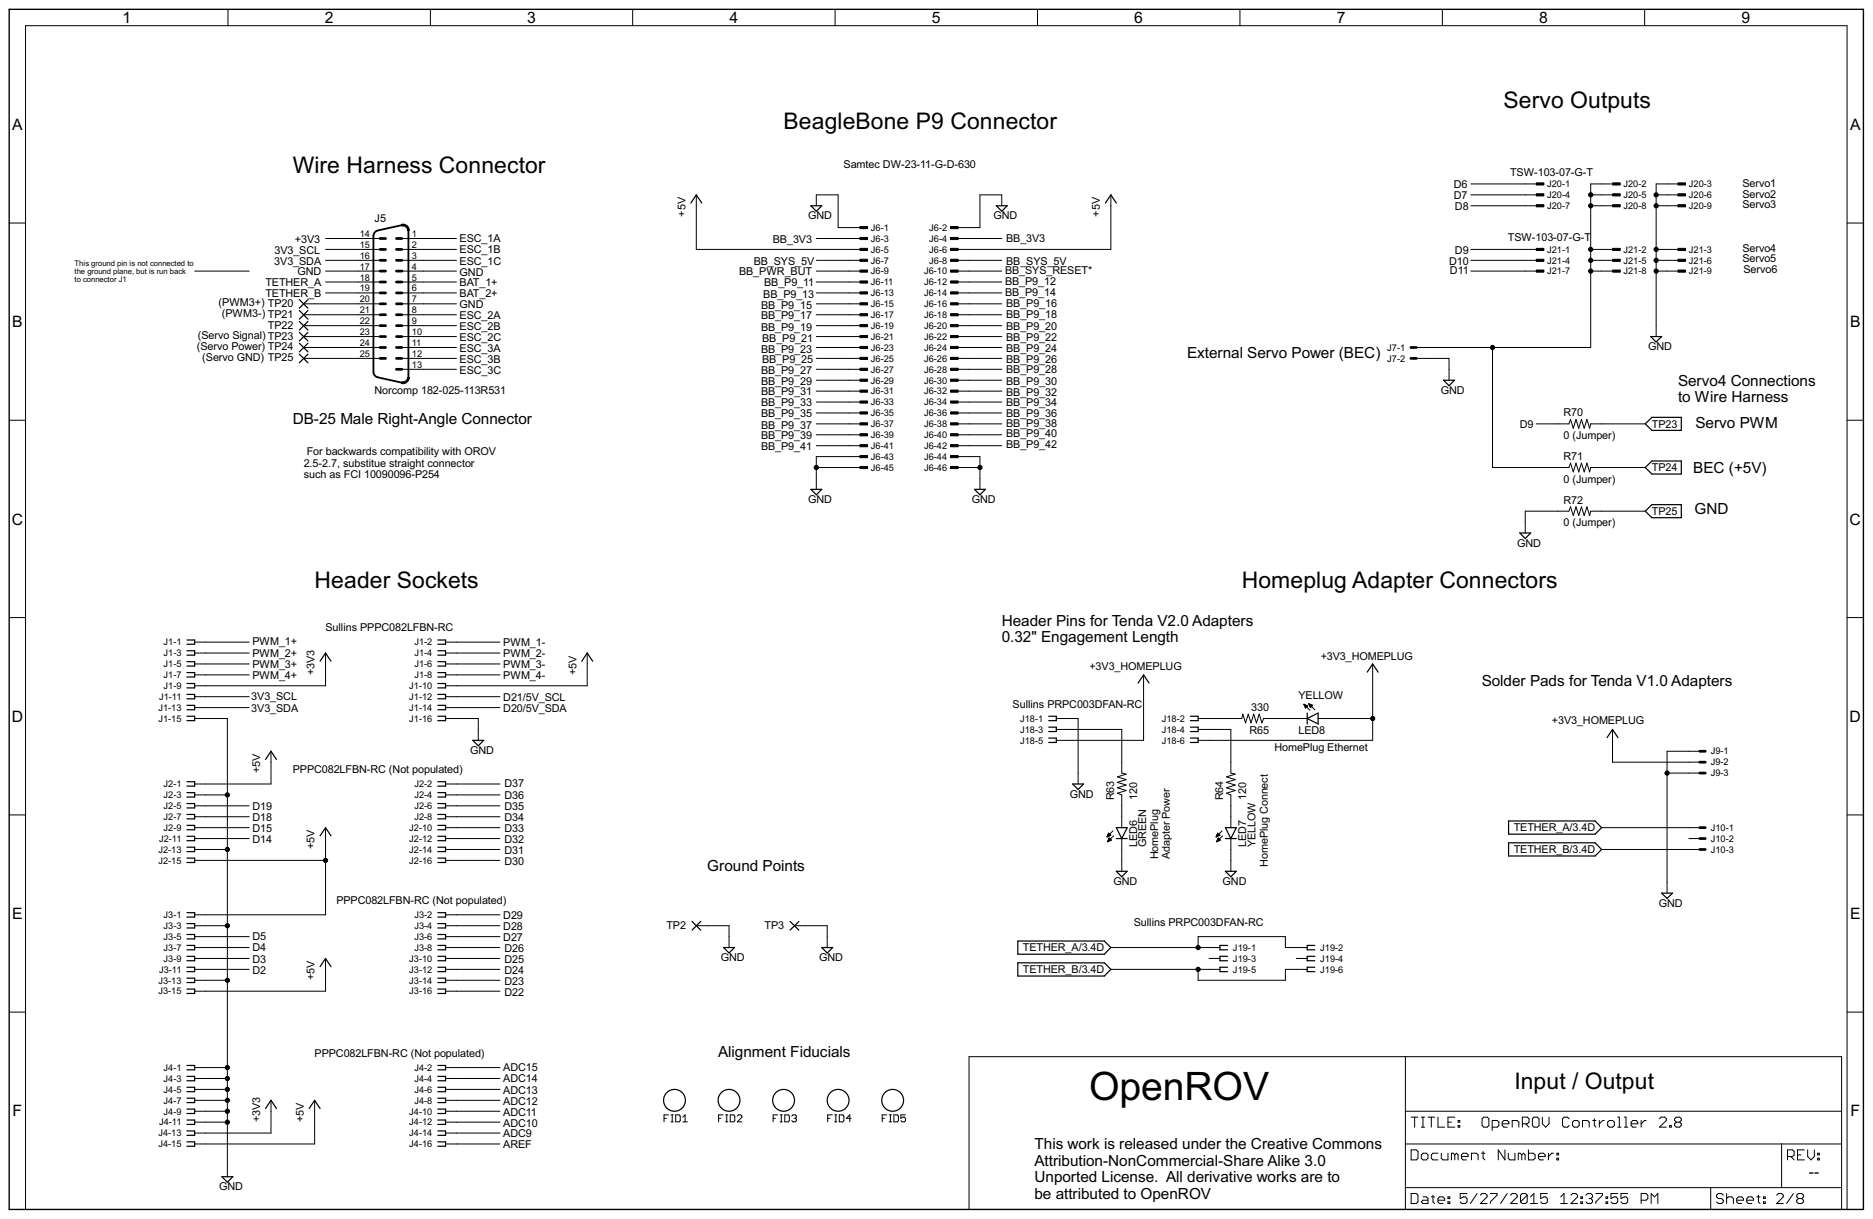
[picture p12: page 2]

Servo1 Servo2 Servo3 Servo4 Servo5 Servo6 External Servo Power (BEC)

This ground pin is not connected to
the ground plane, but is run back
to connector J1

DB-25 Male Right-Angle Connector Header Sockets

0 (Jumper) 0 (Jumper) 0 (Jumper) GND

For backwards compatibility with OROV
2.5-2.7, substitue straight connector such as FCI 10090096-P254

be attributed to OpenROV OpenROV

This work is released under the Creative Commons Attribution-NonCommercial-Share Alike 3.0 Unported License. All derivative works are to

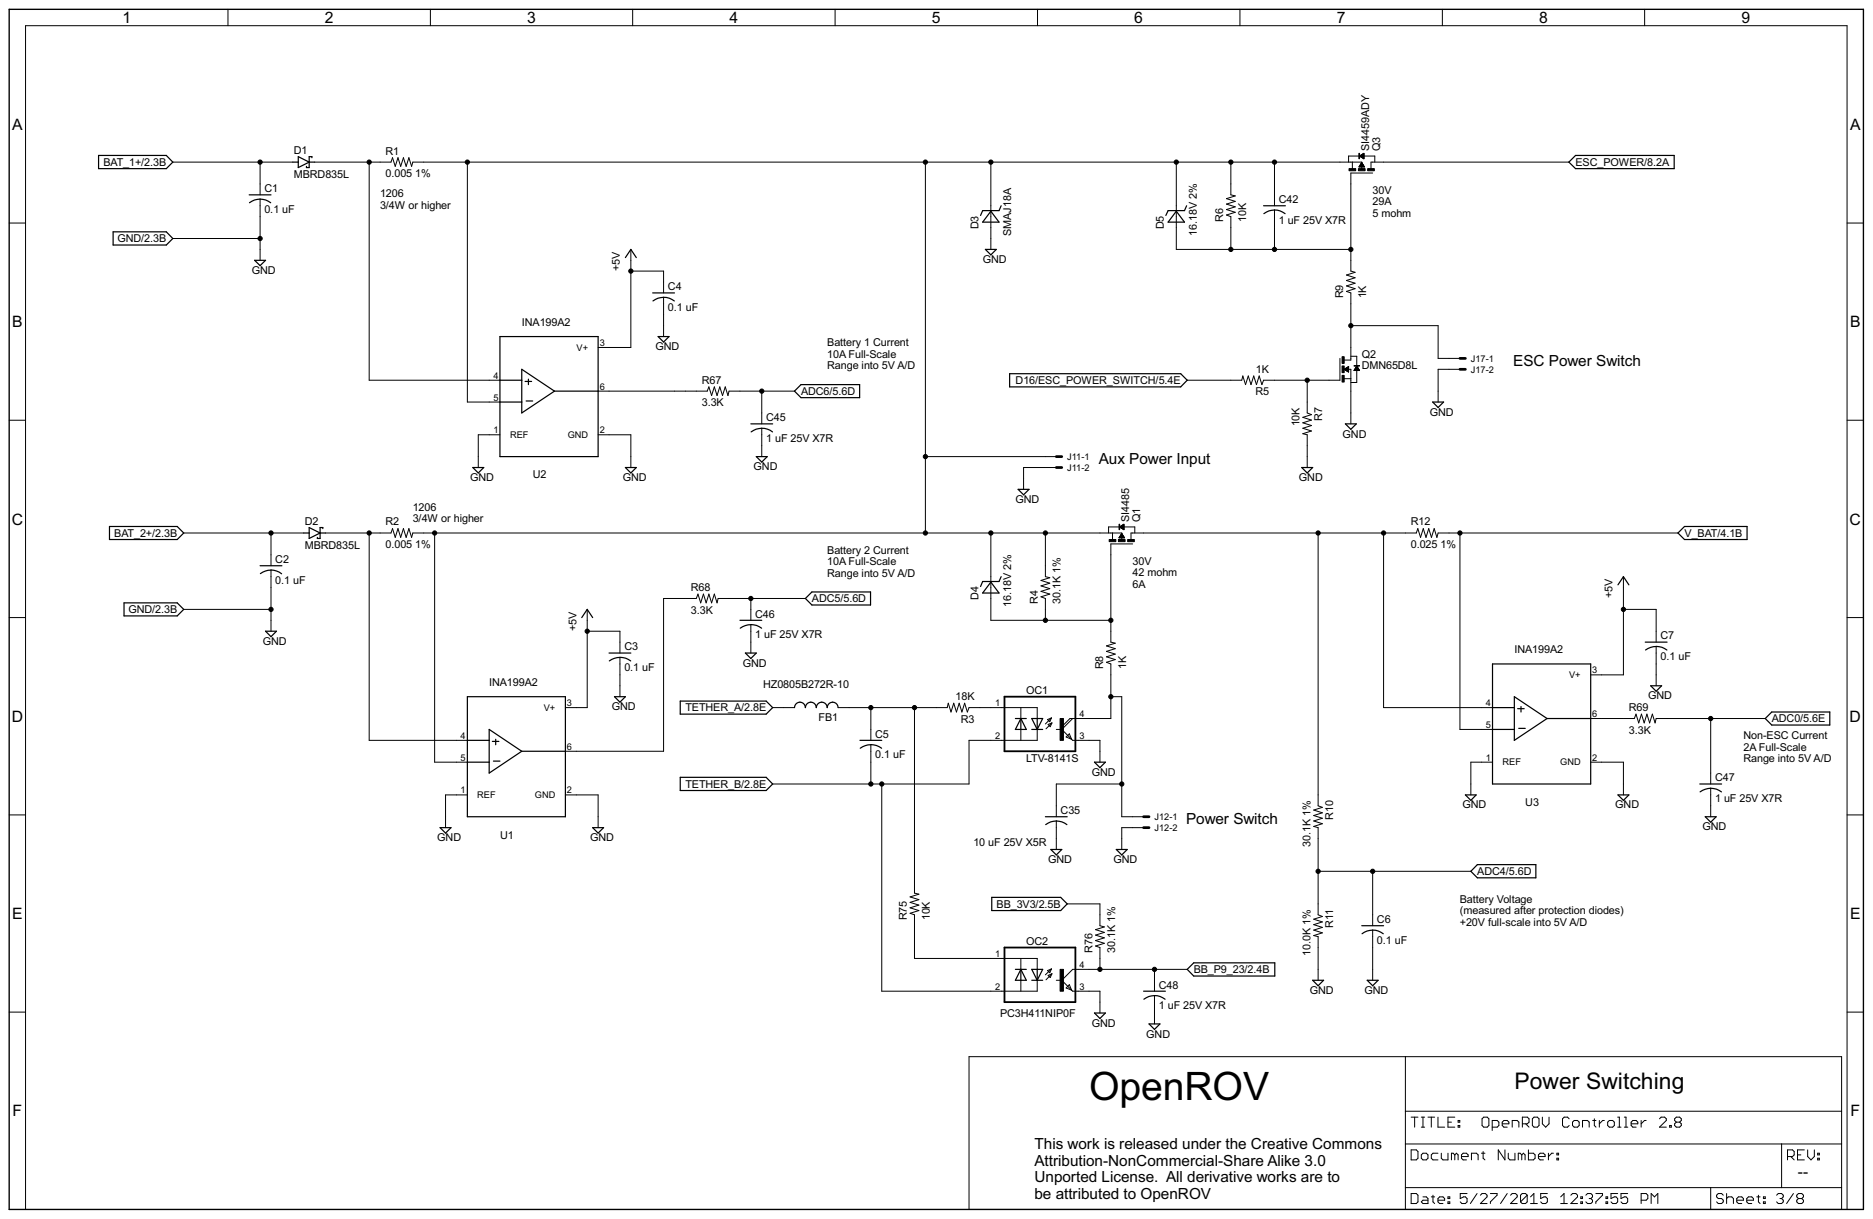
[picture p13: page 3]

Battery 1 Current 10A Full-Scale Range into 5V A/D

Battery 2 Current 10A Full-Scale Range into 5V A/D

Non-ESC Current 2A Full-Scale Range into 5V A/D Power Switch

ADC4/5.6D C6

Battery Voltage
(measured after protection diodes) +20V full-scale into 5V A/D

be attributed to OpenROV OpenROV

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

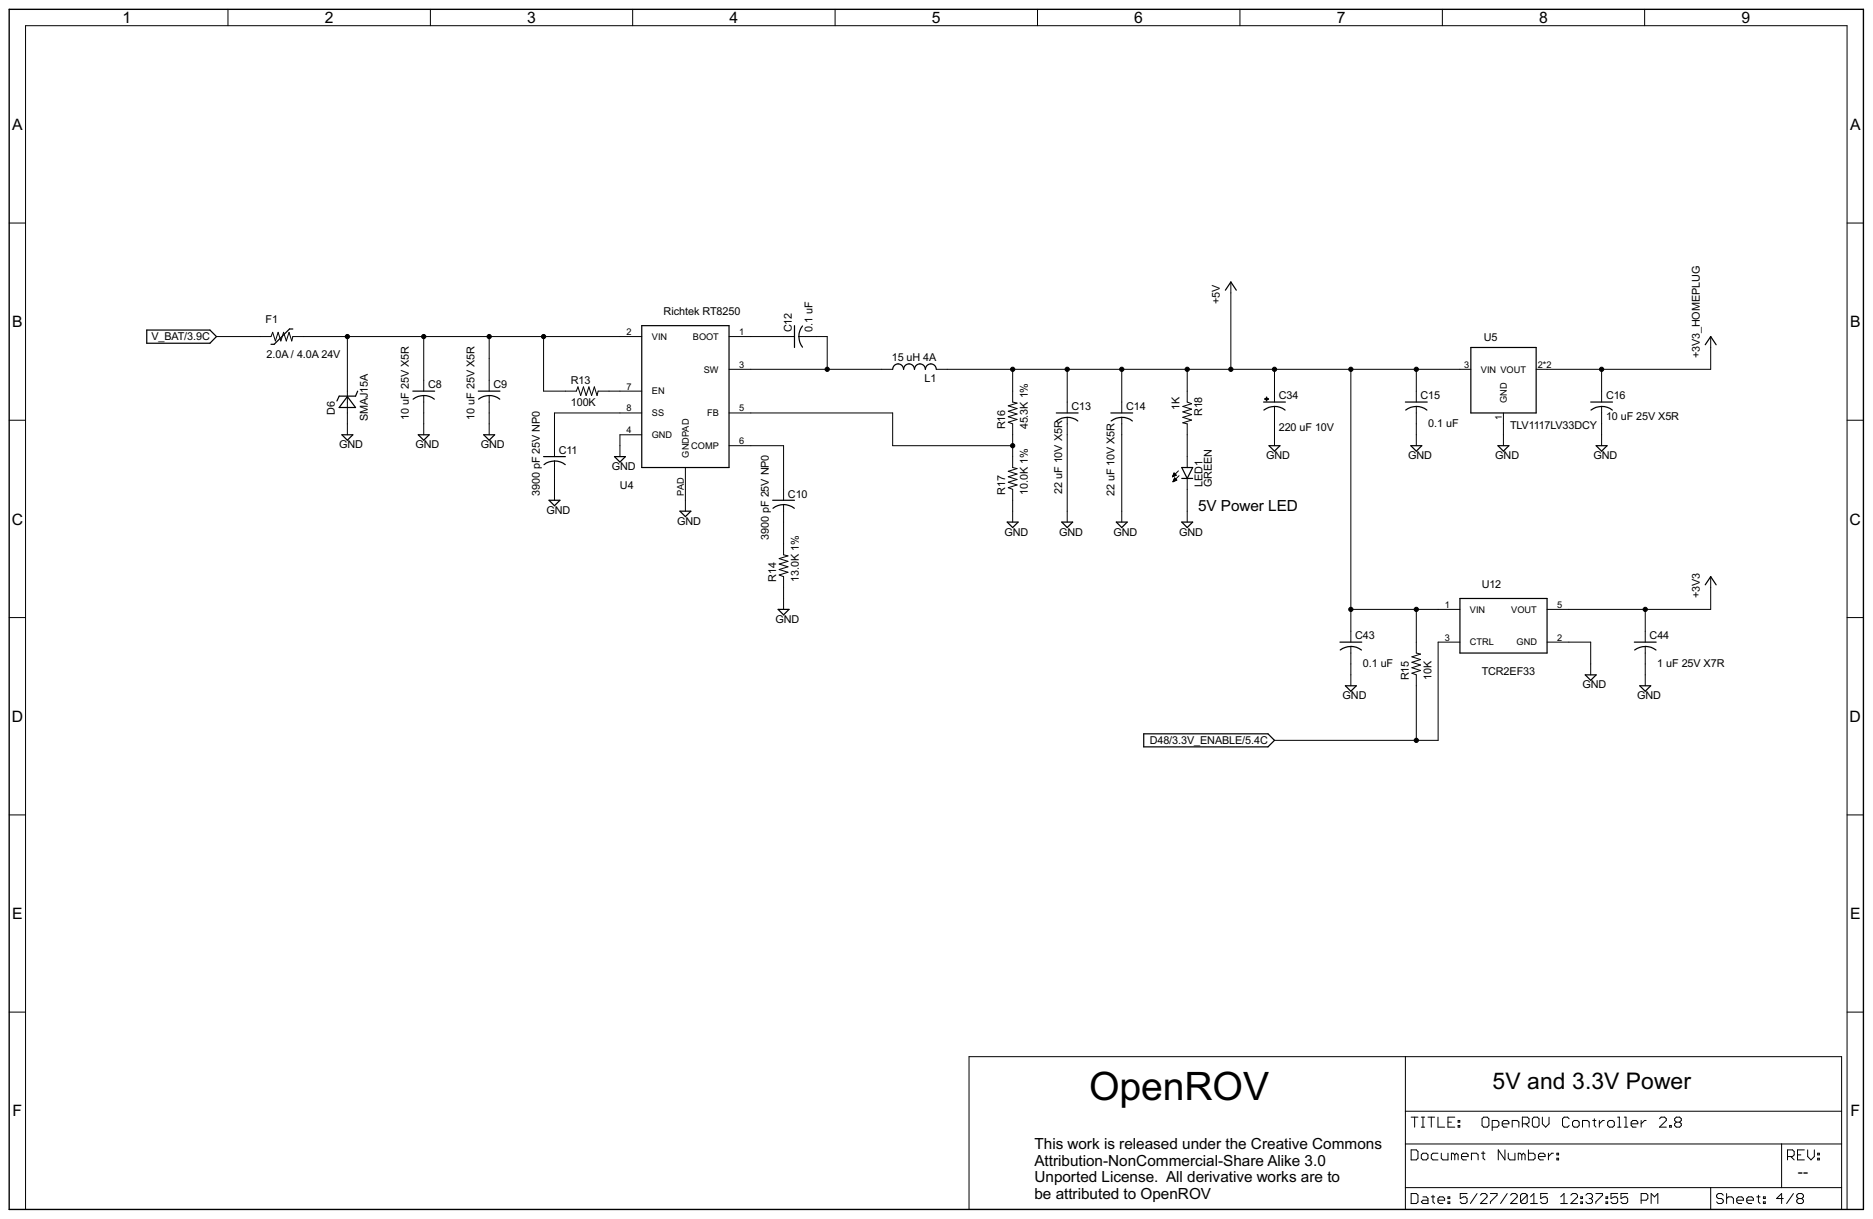
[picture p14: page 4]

be attributed to OpenROV OpenROV

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

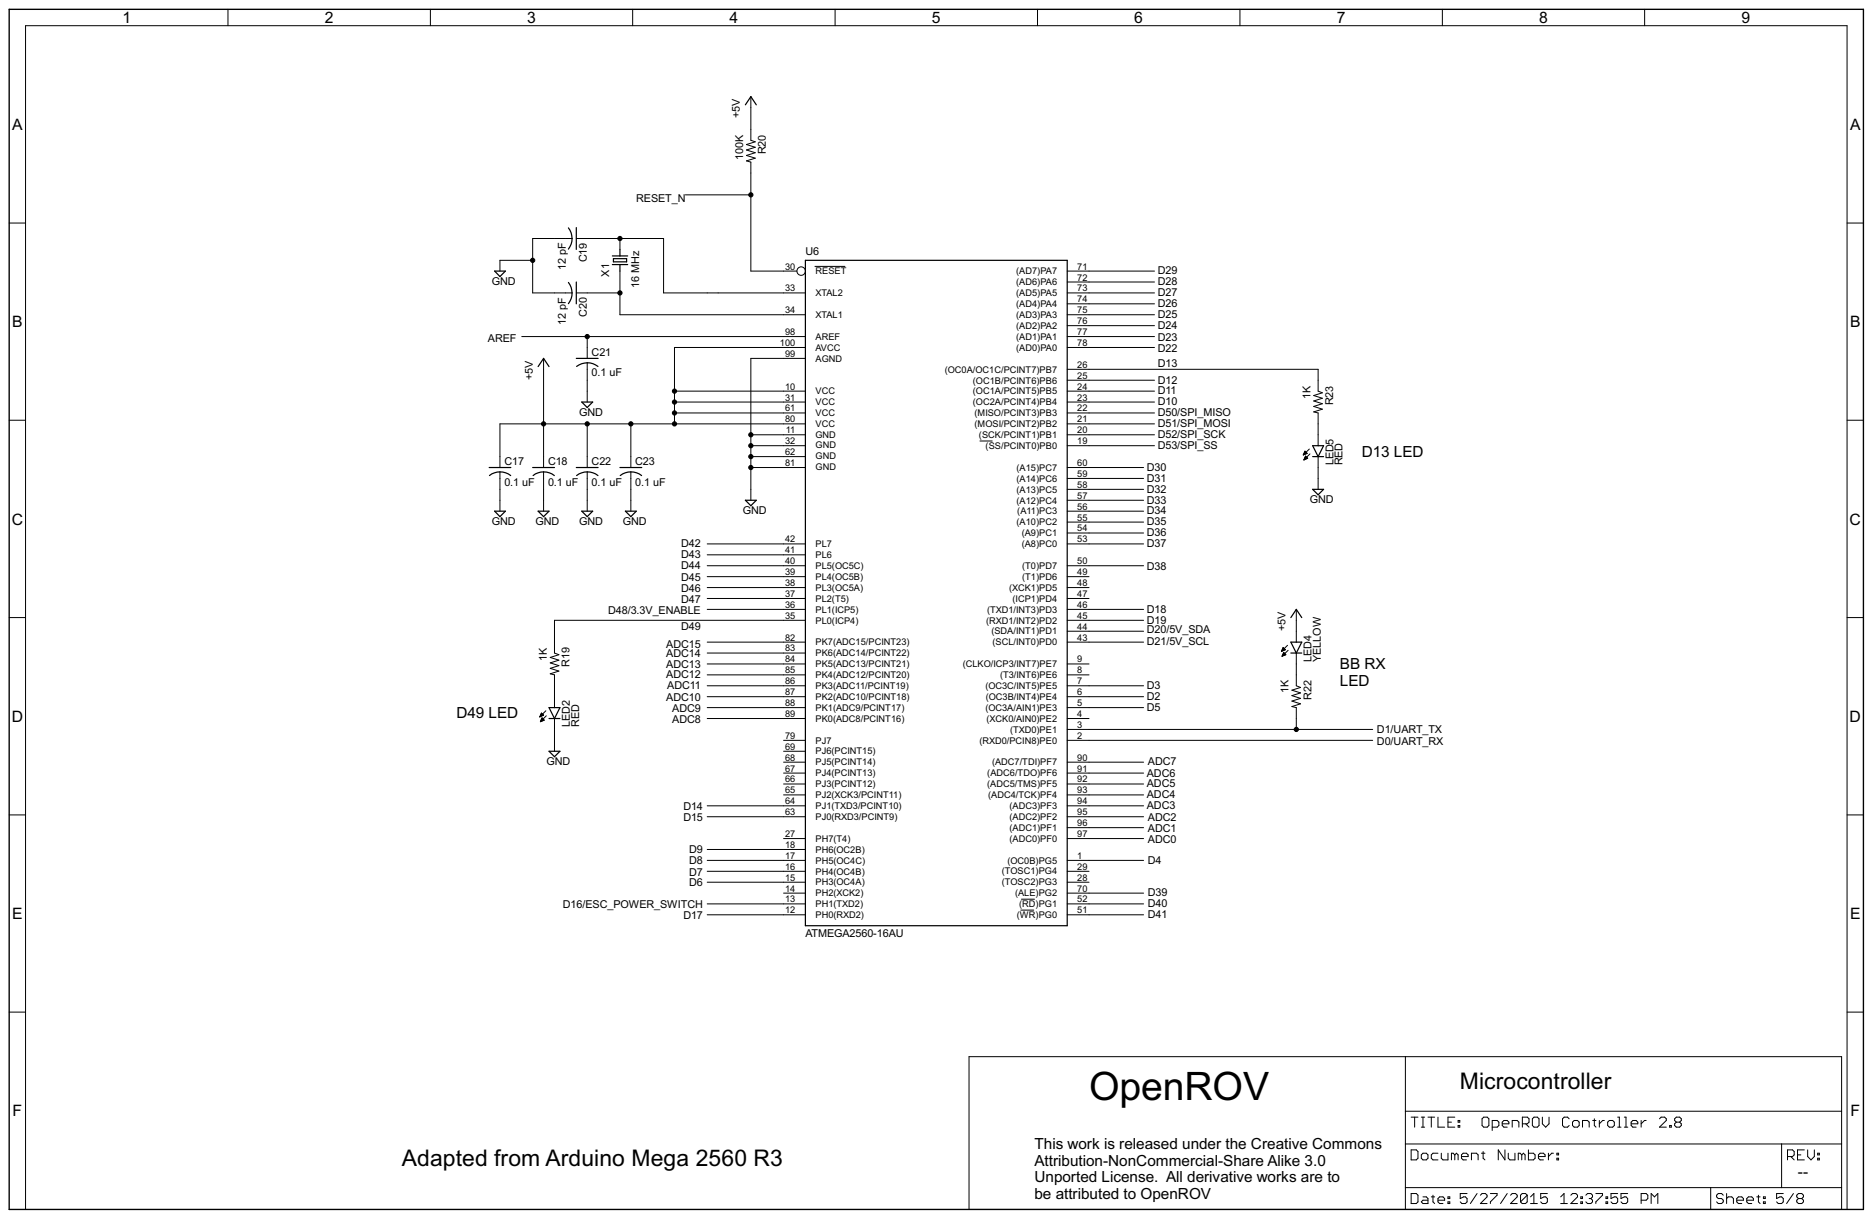
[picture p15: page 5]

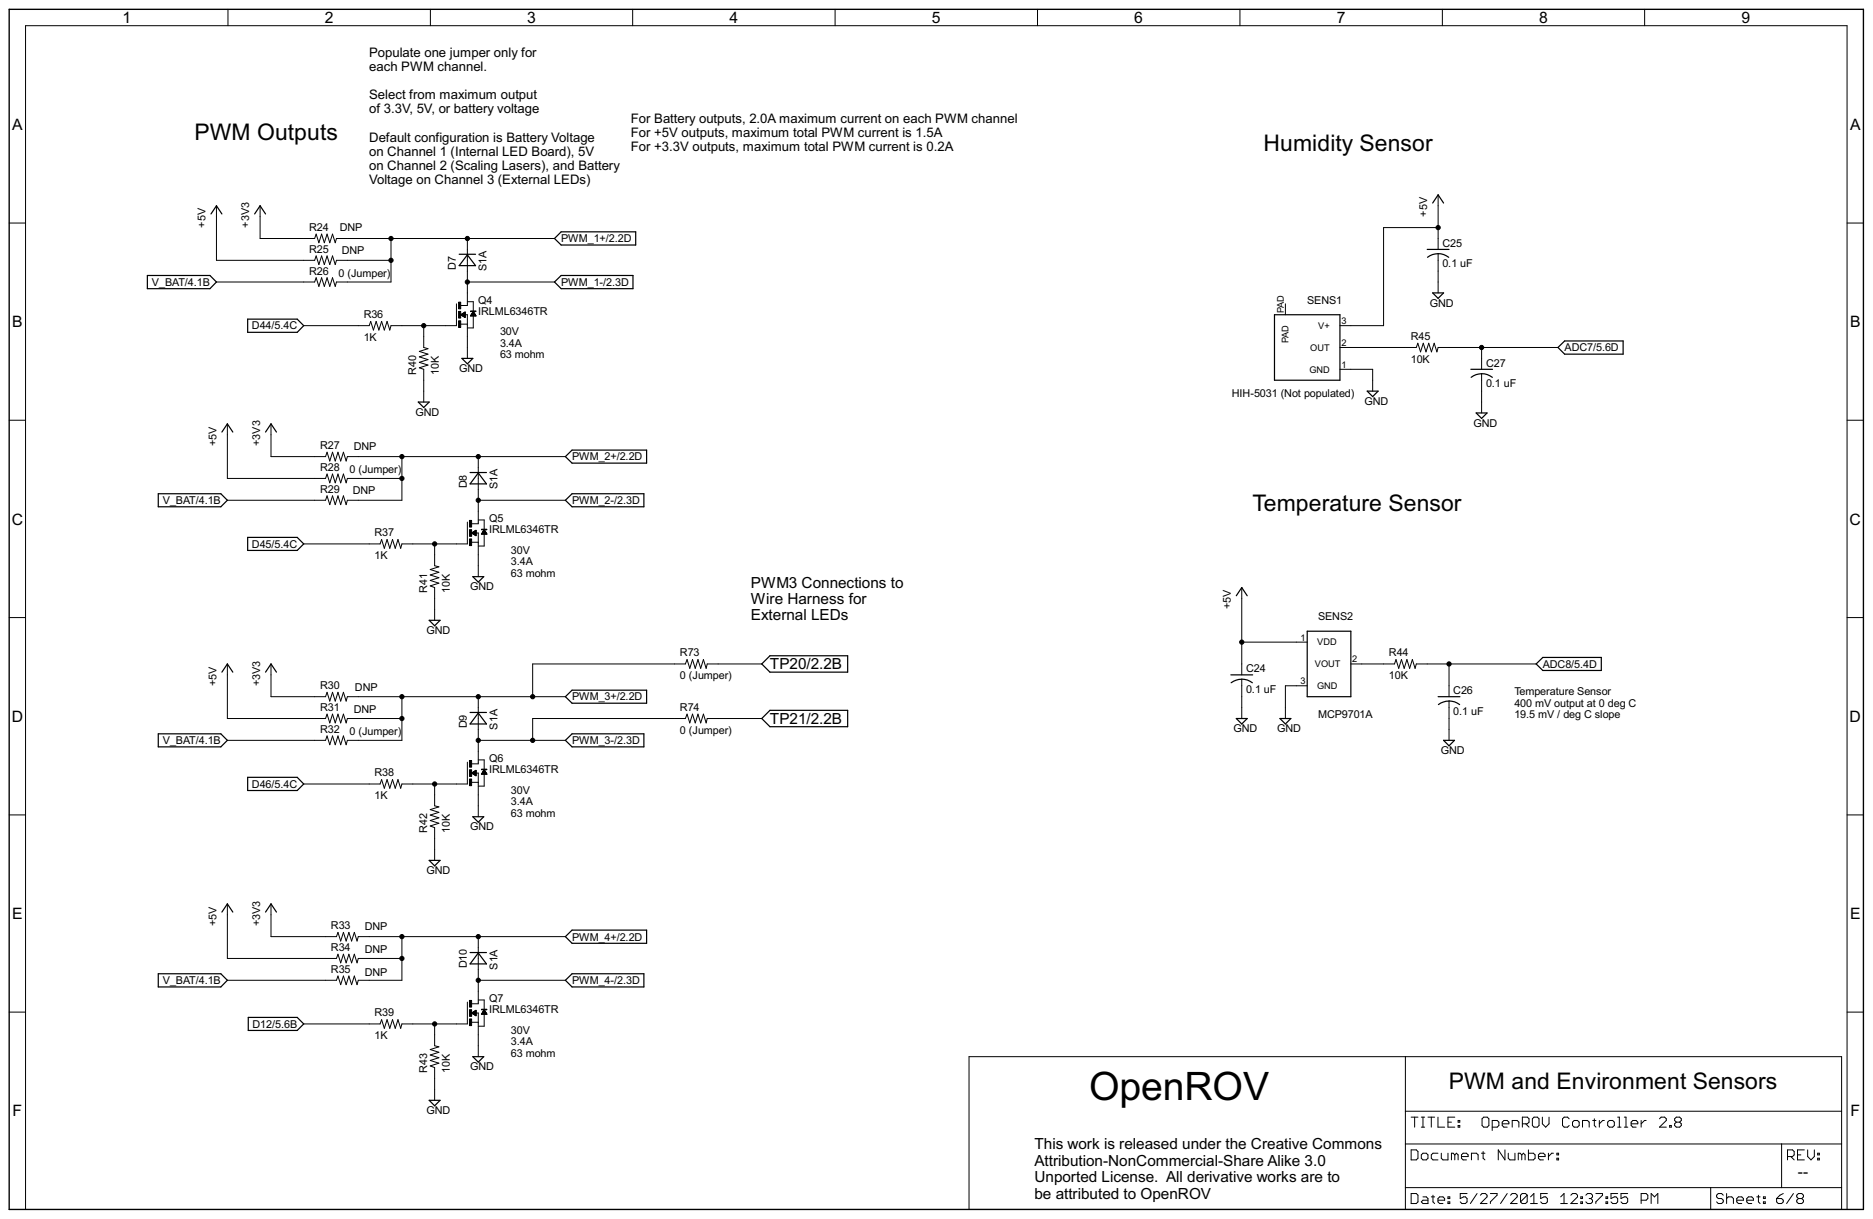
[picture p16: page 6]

Populate one jumper only for each PWM channel. Select from maximum output of 3.3V, 5V, or battery voltage Default configuration is Battery Voltage on Channel 1 (Internal LED Board), 5V

For +3.3V outputs, maximum total PWM current is 0.2A

PWM3 Connections to Wire Harness for External LEDs

Temperature Sensor 400 mV output at 0 deg C

be attributed to OpenROV OpenROV

PWM and Environment Sensors

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

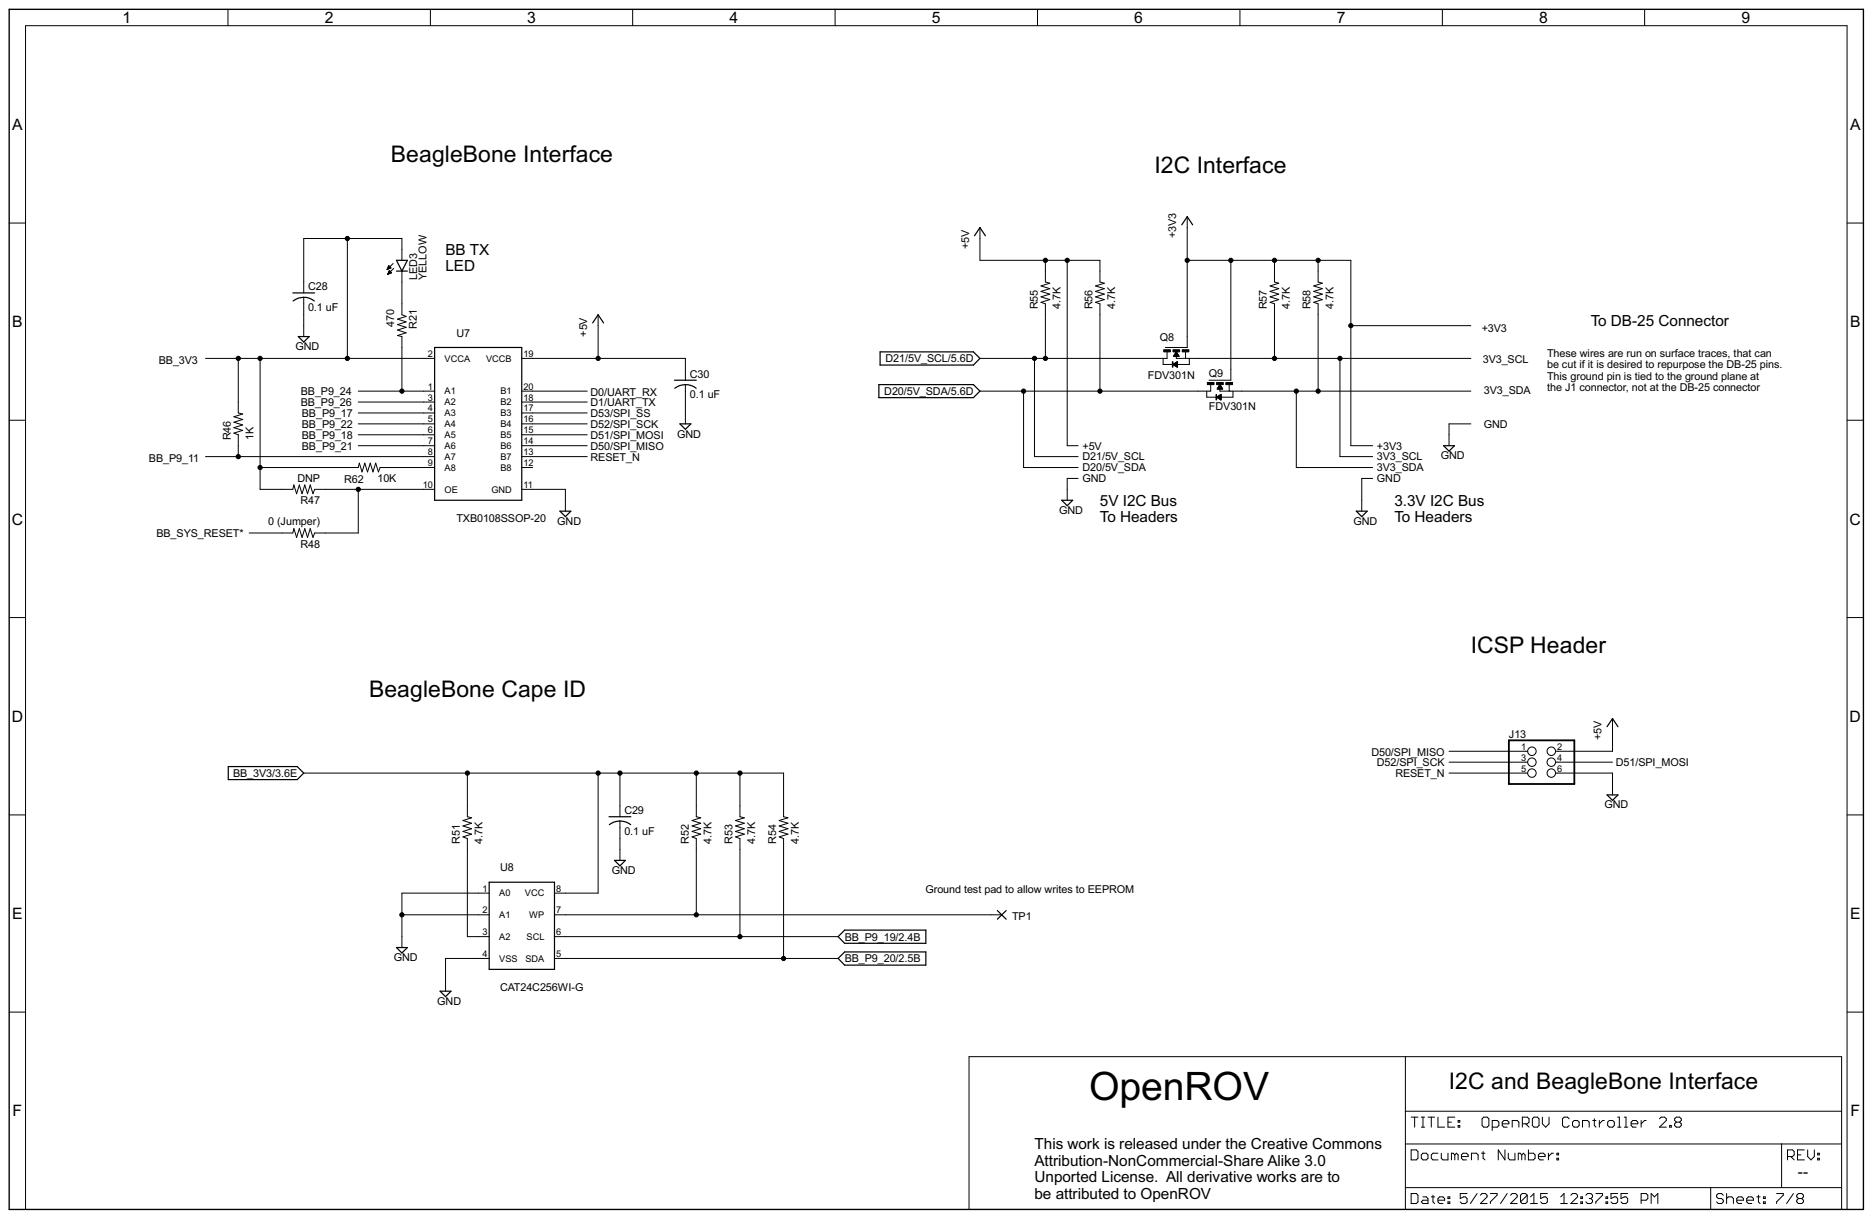
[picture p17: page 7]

These wires are run on surface traces, that can
be cut if it is desired to repurpose the DB-25 pins. This ground pin is tied to the ground plane at

the J1 connector, not at the DB-25 connector

Ground test pad to allow writes to EEPROM

be attributed to OpenROV OpenROV

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

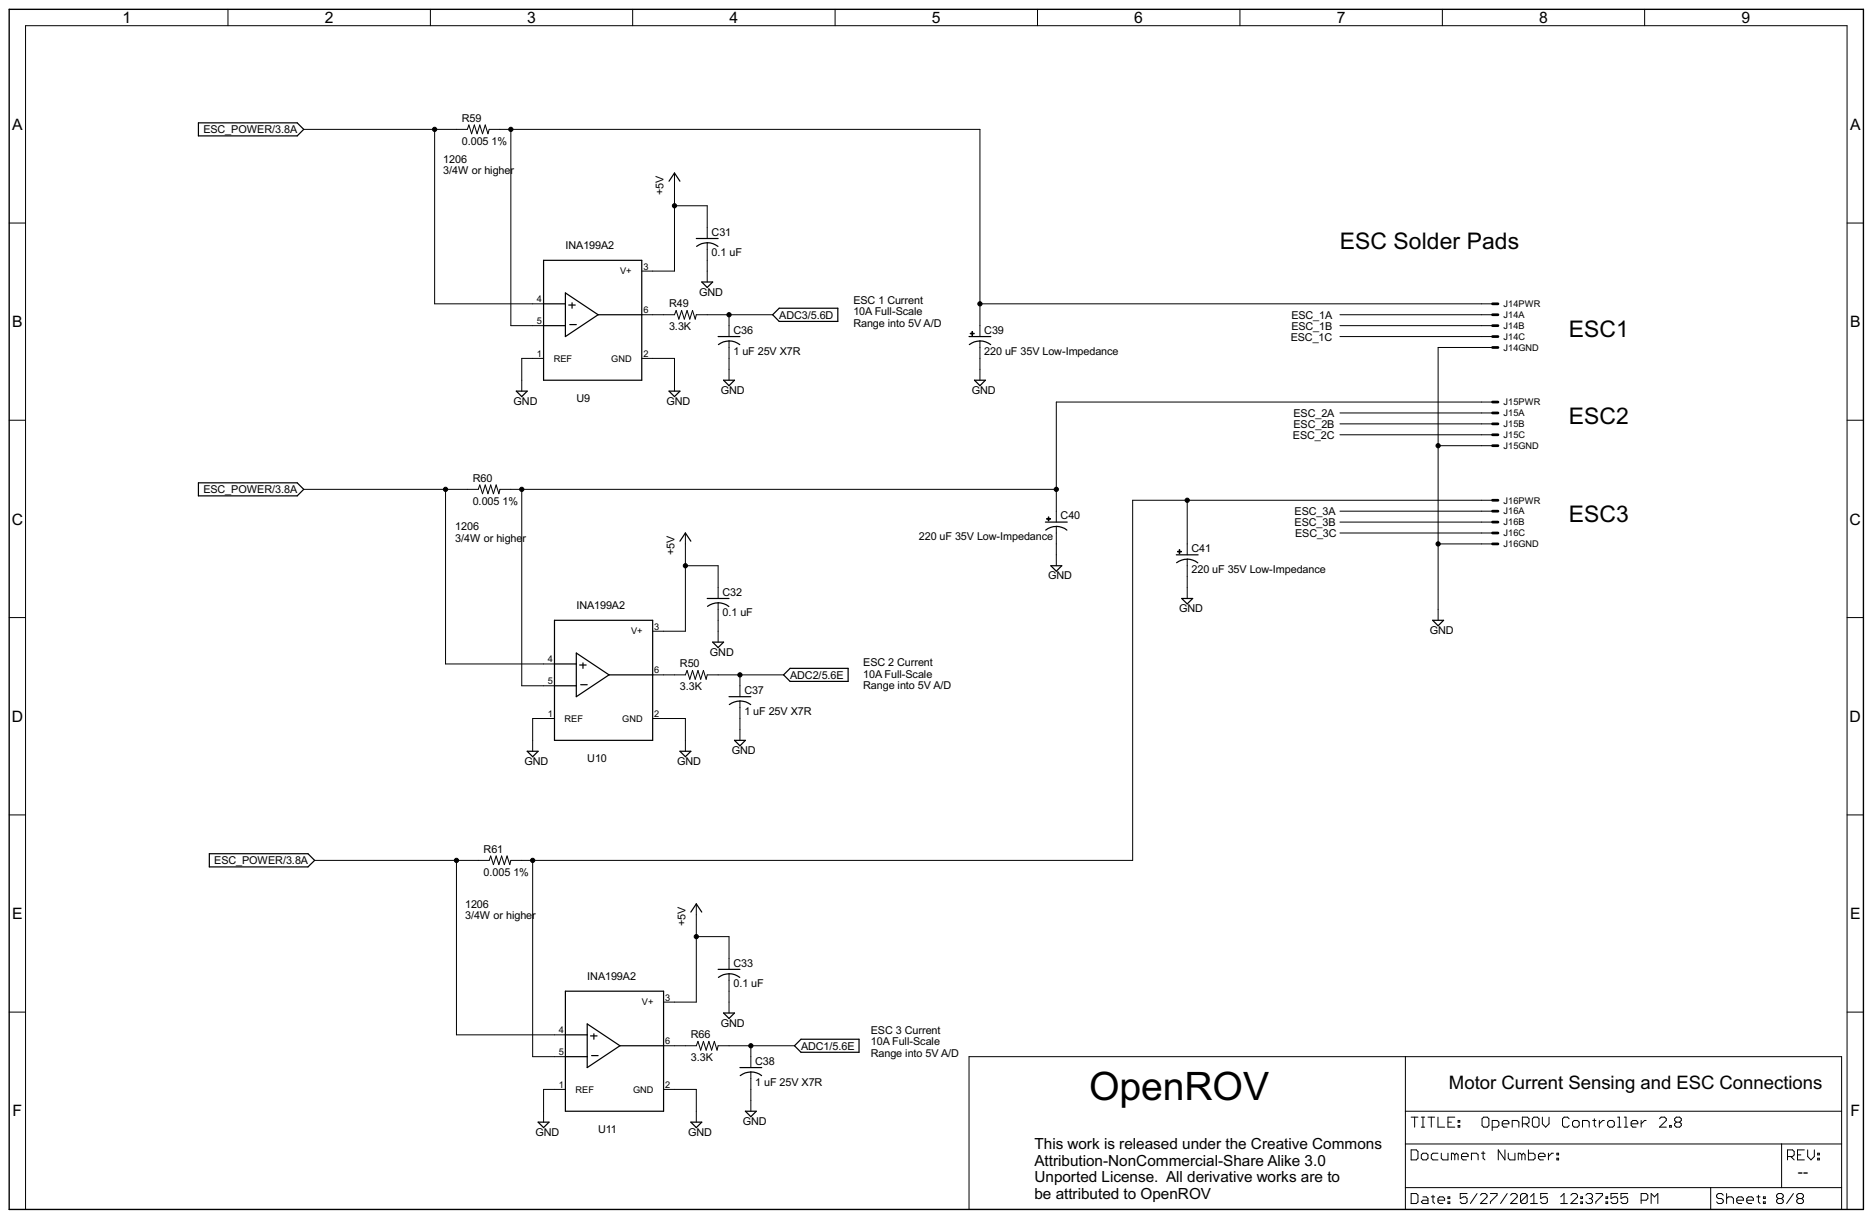
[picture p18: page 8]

ESC 1 Current 10A Full-Scale Range into 5V A/D

ESC 2 Current 10A Full-Scale Range into 5V A/D

ESC 3 Current 10A Full-Scale Range into 5V A/D

be attributed to OpenROV OpenROV

Motor Current Sensing and ESC Connections

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

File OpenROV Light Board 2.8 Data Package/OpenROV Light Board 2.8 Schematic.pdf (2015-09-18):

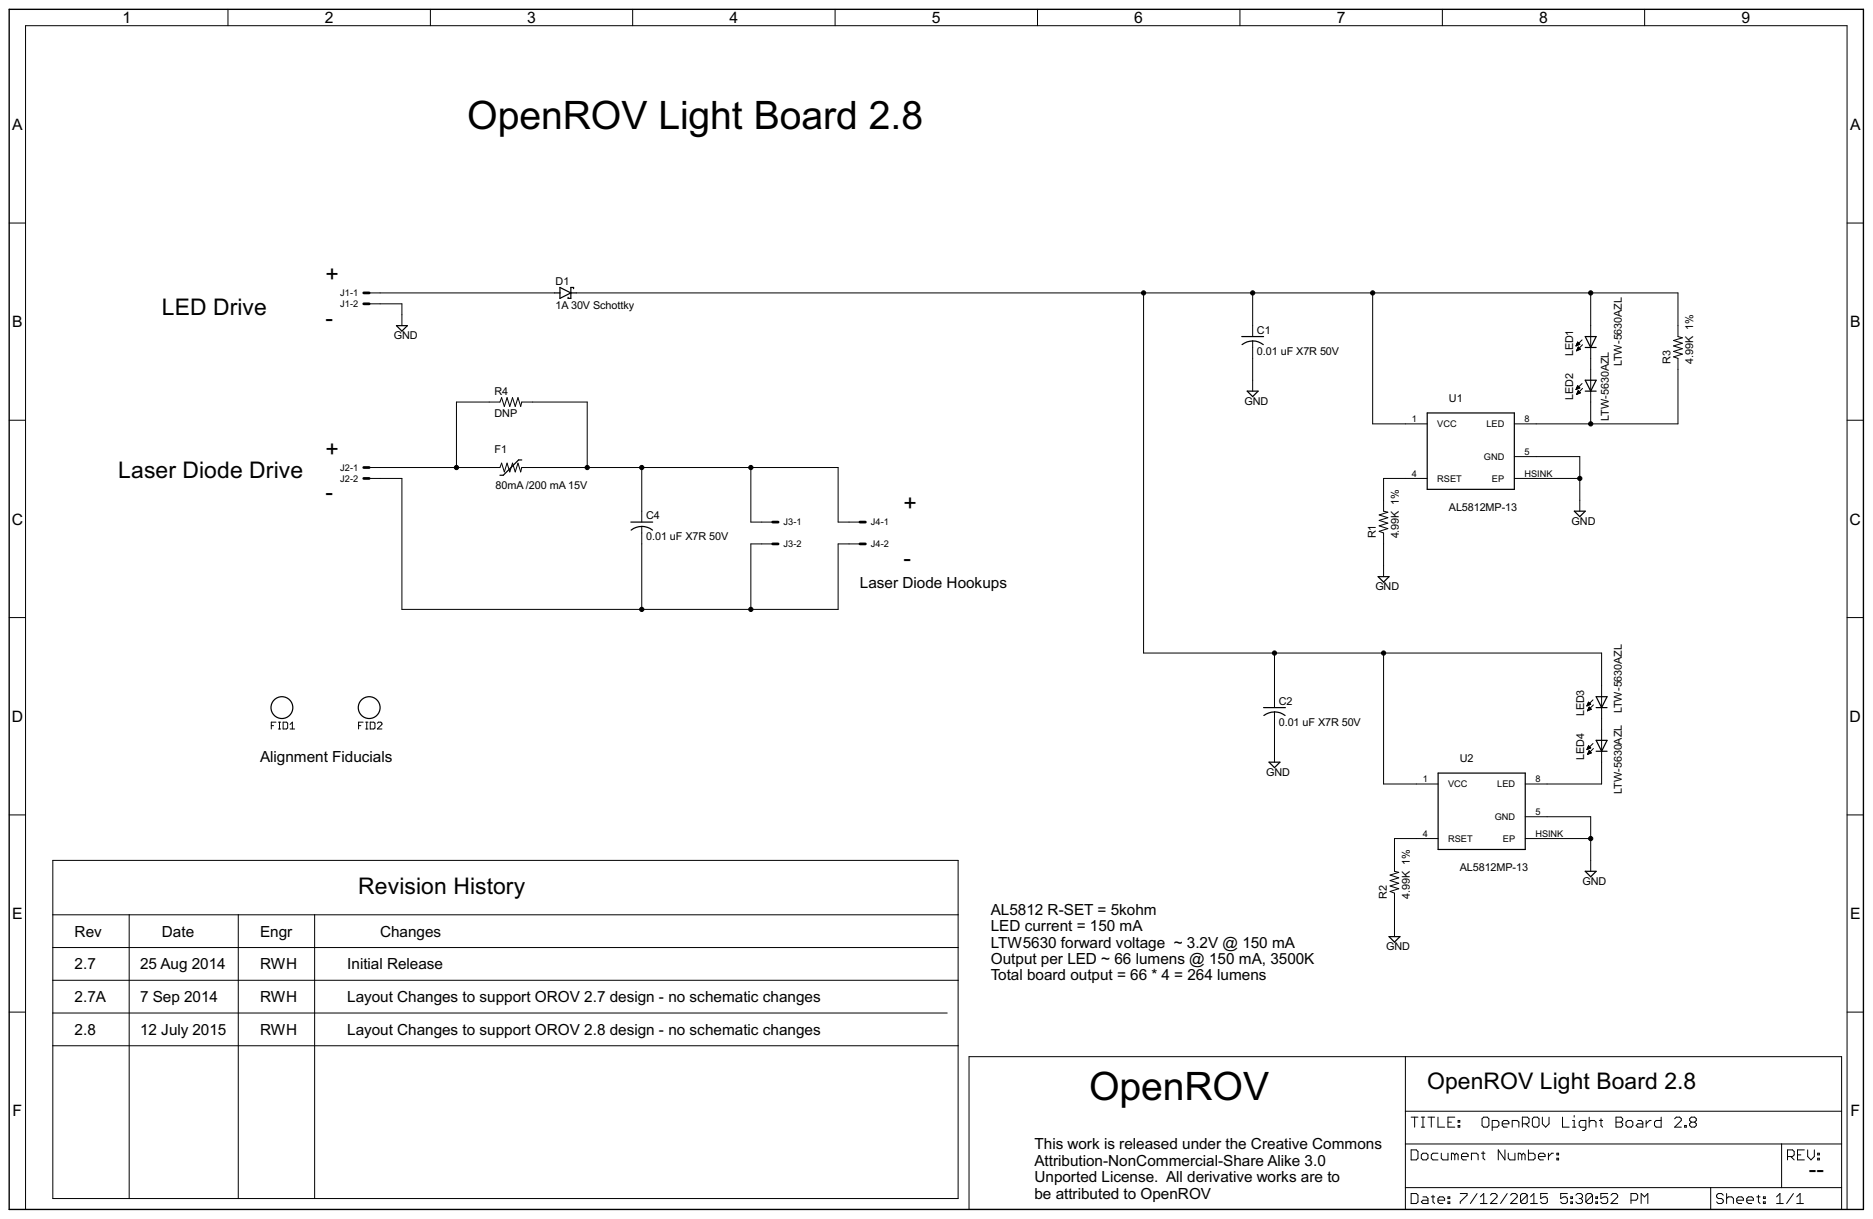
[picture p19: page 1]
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

Rev | 25 Aug 2014 Date | Engr RWH | Initial Release Changes 2.7

Total board output = 66 * 4 = 264 lumens

2.7A | 7 Sep 2014 12 July 2015 | RWH | Layout Changes to support OROV 2.7 design - no schematic changes 2.8 Layout Changes to support OROV 2.8 design - no schematic changes

be attributed to OpenROV OpenROV

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

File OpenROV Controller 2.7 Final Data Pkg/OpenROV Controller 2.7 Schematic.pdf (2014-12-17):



Servo Outputs

Servo1 Servo2 Servo3 Servo4 Servo5 Servo6 External Servo Power (BEC)

This ground pin is not connected to
the ground plane, but is run back
to connector J1

DB-25 Male Vertical Connector Header Sockets

be attributed to OpenROV OpenROV

This work is released under the Creative Commons Attribution-NonCommercial-Share Alike 3.0 Unported License. All derivative works are to


ADC6/5.6D
Battery 1 Current 10A Full-Scale Range into 5V A/D

ADC5/5.6D
Battery 2 Current 10A Full-Scale Range into 5V A/D

Non-ESC Current 2A Full-Scale Range into 5V A/D Power Switch

Battery Voltage
(measured after protection diodes) +20V full-scale into 5V A/D

be attributed to OpenROV OpenROV

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


be attributed to OpenROV OpenROV

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



Populate one jumper only for each PWM channel. Select from maximum output of 3.3V, 5V, or battery voltage Default configuration is Battery Voltage

For +3.3V outputs, maximum total PWM current is 0.2A

on Channel 1 (LED Modules), and 5V

Temperature Sensor 400 mV output at 0 deg C

be attributed to OpenROV OpenROV

PWM and Environment Sensors

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


These wires are run on surface traces, that can
be cut if it is desired to repurpose the DB-25 pins. This ground pin is tied to the ground plane at

the J1 connector, not at the DB-25 connector

Remove resistor for write-protect

be attributed to OpenROV OpenROV

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


ESC 1 Current 10A Full-Scale Range into 5V A/D

ESC 2 Current 10A Full-Scale Range into 5V A/D

ESC 3 Current 10A Full-Scale Range into 5V A/D

be attributed to OpenROV OpenROV

Motor Current Sensing and ESC Connections

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

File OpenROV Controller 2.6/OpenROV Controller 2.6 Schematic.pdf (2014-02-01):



Servo Outputs

Servo1 Servo2 Servo3 Servo4 Servo5 Servo6 External Servo Power (BEC)

This ground pin is not connected to
the ground plane, but is run back
to connector J1

DB-25 Male Vertical Connector Header Sockets

be attributed to OpenROV OpenROV

This work is released under the Creative Commons Attribution-NonCommercial-Share Alike 3.0 Unported License. All derivative works are to


ADC6/5.6D
Battery 1 Current 10A Full-Scale Range into 5V A/D

ADC5/5.6D
Battery 2 Current 10A Full-Scale Range into 5V A/D

Non-ESC Current 2A Full-Scale Range into 5V A/D Power Switch

Battery Voltage
(measured after protection diodes) +20V full-scale into 5V A/D

be attributed to OpenROV OpenROV

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


1 uF 50V X5R GND GND GND

Coilcraft Inductor 15 uH 0.04 ohm 3.5A

be attributed to OpenROV OpenROV

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

-- +5V Supply Adapted from the CircuitCo OpenROV Cape




These wires are run on surface traces, that can
be cut if it is desired to repurpose the DB-25 pins. This ground pin is tied to the ground plane at

the J1 connector, not at the DB-25 connector

Remove resistor for write-protect

be attributed to OpenROV OpenROV

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


ESC 1 Current 10A Full-Scale Range into 5V A/D

ESC 2 Current 10A Full-Scale Range into 5V A/D

ESC 3 Current 10A Full-Scale Range into 5V A/D

be attributed to OpenROV OpenROV

Motor Current Sensing and ESC Connections

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

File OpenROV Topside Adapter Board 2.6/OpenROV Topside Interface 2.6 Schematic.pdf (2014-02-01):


Optional Power Switch Connector

for Tenda V2.0 Homeplug Adapter Power

Header socket
for Tenda V2.0 Homeplug Adapter

1.) 5V bias on tether is used to turn ROV power on
2.) Remove Resistor R1 to disable auto-power-on
3.) Remove Resistors R1 and R2 to electrically isolate tether from USB
4.) To add power switch to topside box, remove resistor R6 and connect
switch across J5

be attributed to OpenROV OpenROV

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

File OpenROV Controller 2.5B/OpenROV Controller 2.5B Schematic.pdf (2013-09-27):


A | 20 Aug 2013 | RWH | Prototype Batch. Revised J6 connector orientation. Changed BB node names. Revised C11, C15, and U5 and added C34 to avoid +5V and +3.3V brownout when switching ESCs on. Revised ESC mounting holes. Revised LED colors. Revised silkscreen. Added weak Arduino reset pullup for standalone operation. Added cap slot C35 to hold vehicle on if noisy tether connection. Added bypass points J17 for ESC power switch. Arduino reset function moved from

2 Sep 2013 | RWH | BB pin 13 to BB pin 11. B First production batch. J6 changed from socket to male board stacker. 4th mounting hole added to board. Revised fiducial locations. Inverted logical case of UART LEDs. BB TX LED moved from Arduino space to BB space. Board ID EEPROM circuitry DNP.

Cover Page
Input / Output
Power Switching
5V and 3.3V Power
Microcontroller (Arduino Mega compatible)
PWM and Environment Sensors
I2C and BeagleBone Interface

be attributed to OpenROV OpenROV

This work is released under the Creative Commons Attribution-NonCommercial-Share Alike 3.0 Unported License. All derivative works are to


This ground pin is not connected to
the ground plane, but is run back
to connector J1

Servo1 Servo2 Servo3 Servo4 Servo5 Servo6 Servo Power Attachment (BEC)

DB-25 Male Vertical Connector Header Sockets

be attributed to OpenROV OpenROV

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


ESC Power Switch Bypass

ADC6/5.6D
Battery 1 Current 10A Full-Scale Range into 5V A/D

ADC5/5.6D
Battery 2 Current 10A Full-Scale Range into 5V A/D

Non-ESC Current 2A Full-Scale Range into 5V A/D Power Switch

Battery Voltage
(measured after protection diodes) +20V full-scale into 5V A/D

be attributed to OpenROV OpenROV

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


1 uF 50V X5R GND GND GND

Coilcraft Inductor 15 uH 0.04 ohm 3.5A

be attributed to OpenROV OpenROV

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

+5V Supply Adapted from the CircuitCo OpenROV Cape




These wires are run on surface traces, that can
be cut if it is desired to repurpose the DB-25 pins. This ground pin is tied to the ground plane at

the J1 connector, not at the DB-25 connector

Ground this test point to disable write-protect

be attributed to OpenROV OpenROV

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


ESC 1 Current 10A Full-Scale Range into 5V A/D

ESC 2 Current 10A Full-Scale Range into 5V A/D

be attributed to OpenROV OpenROV

Motor Current Sensing and ESC Connections

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


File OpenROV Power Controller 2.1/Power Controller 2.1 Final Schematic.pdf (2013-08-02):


This work is licensed under the Creative Commons Attribution-NonCommercial-Share Alike 3.0 Unported License. All derivative works are to be attributed to OpenROV.

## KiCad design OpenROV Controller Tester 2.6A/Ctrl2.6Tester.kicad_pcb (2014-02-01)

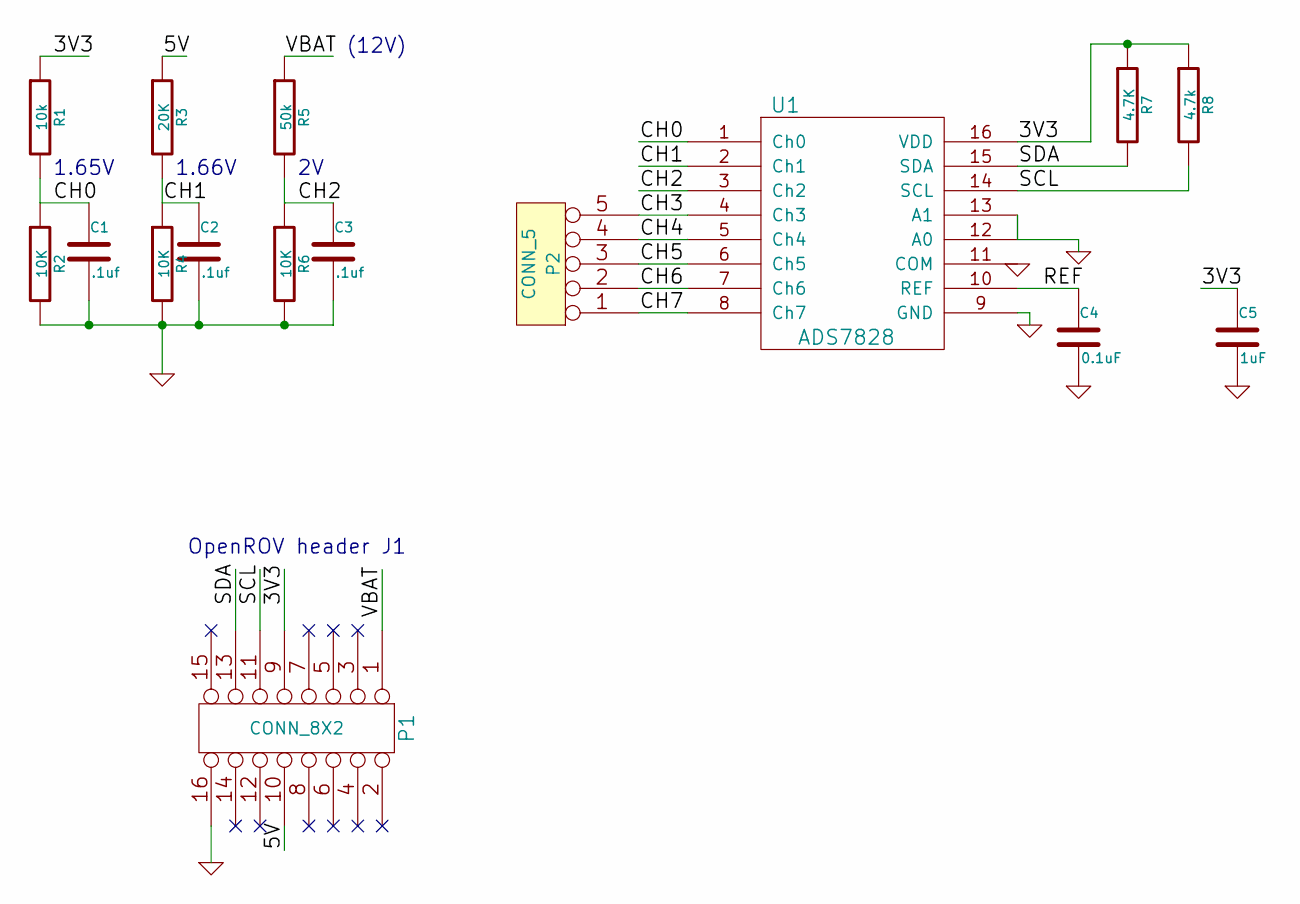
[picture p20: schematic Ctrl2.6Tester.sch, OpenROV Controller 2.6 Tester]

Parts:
C1, C2, C3: .1uf
C4: 0.1uF
C5: 1uF
P1: CONN_8X2
P2: CONN_5
R1: 10k
R2, R4, R6: 10K
R3: 20K
R5: 50k
R7: 4.7K
R8: 4.7k
U1: ADS7828

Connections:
/3V3: C5.1, P1.9, R1.1, R7.1, R8.1, U1.16 (VDD)
/5V: P1.10, R3.1
/CH0: C1.1, R1.2, R2.1, U1.1 (Ch0)
/CH1: C2.1, R3.2, R4.1, U1.2 (Ch1)
/CH2: C3.1, R5.2, R6.1, U1.3 (Ch2)
/CH3: P2.5, U1.4 (Ch3)
/CH4: P2.4, U1.5 (Ch4)
/CH5: P2.3, U1.6 (Ch5)
/CH6: P2.2, U1.7 (Ch6)
/CH7: P2.1, U1.8 (Ch7)
/REF: C4.1, U1.10 (REF)
/SCL: P1.11, R8.2, U1.14 (SCL)
/SDA: P1.13, R7.2, U1.15 (SDA)
/VBAT: P1.1, R5.1
GND: C1.2, C2.2, C3.2, C4.2, C5.2, P1.16, R2.2, R4.2, R6.2, U1.9 (GND), U1.11 (COM), U1.12 (A0), U1.13 (A1)

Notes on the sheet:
OpenROV header J1
1.65V
1.66V
(12V)

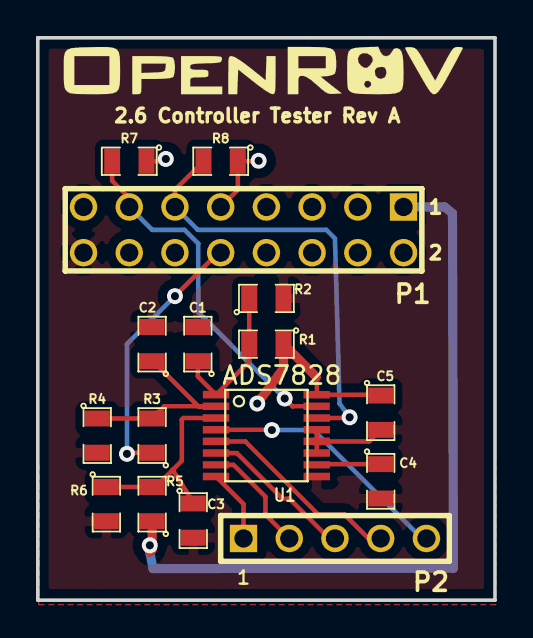
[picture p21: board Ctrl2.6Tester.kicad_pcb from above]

Board: 2 copper layers, 25.4 x 31.2 mm, 15 parts (0 on the bottom side), 13 nets.

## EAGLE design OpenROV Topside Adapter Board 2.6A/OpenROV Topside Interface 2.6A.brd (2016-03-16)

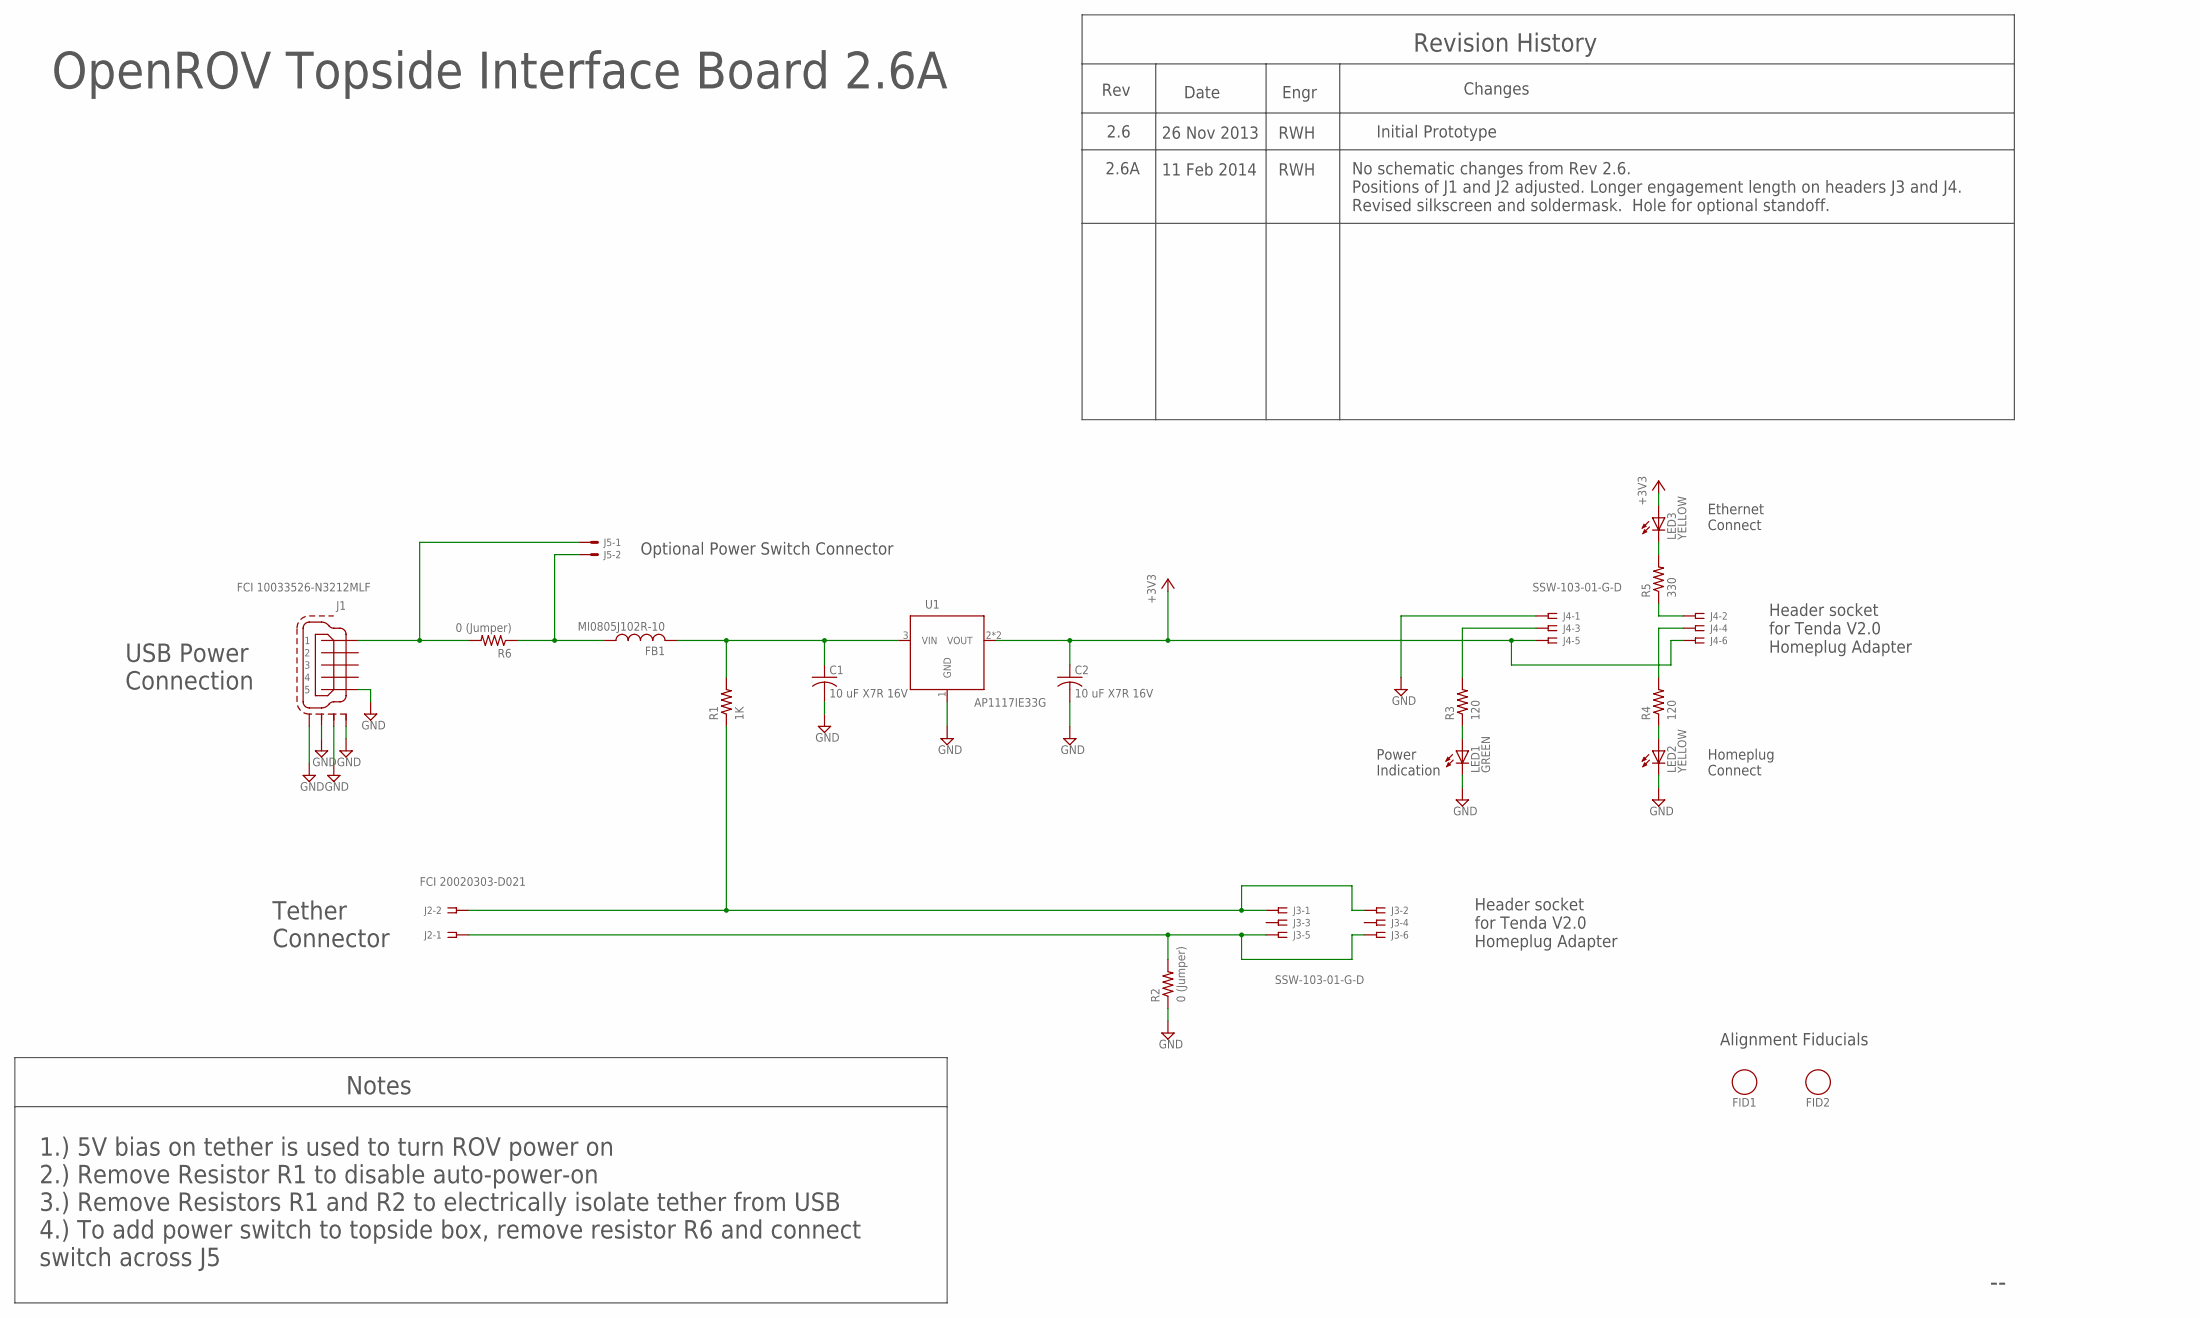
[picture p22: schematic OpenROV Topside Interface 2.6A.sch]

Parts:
C1, C2: 10 uF X7R 16V; R1206
FB1: MI0805J102R-10; R0805
FID1, FID2: FIDUCIAL_1
J1: FCI 10033526-N3212MLF; USB_MINI-B_SM
J2: FCI 20020303-D021; FCI_09-381_2PL
J3, J4: SSW-103-01-G-D; SSW-103-02-S-D
J5: HDR_1X2X0.100-ALT_SILK; 22-23-2021_ALT_SILK
LED1: GREEN; LED_0805_BOTTOM_MT(OSRAM)
LED2, LED3: YELLOW; LED_0805_BOTTOM_MT(OSRAM)
R1: 1K; R0805
R2, R6: 0 (Jumper); R0805
R3, R4: 120; R0805
R5: 330; R0805
U1: AP1117IE33G; SOT223

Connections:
+3V3: C2.1, J4.5, J4.6, LED3.A, U1.2 (VOUT), U1.4 (VOUT)
GND: C1.2, C2.2, J1.5, J1.M1 (S1), J1.M2 (S2), J1.M3 (S3), J1.M4 (S4), J4.1, LED1.C, LED2.C, R2.1, U1.1 (GND)
unnamed: J2.1A, J2.1B, J3.5, J3.6, R2.2
unnamed: J2.2A, J2.2B, J3.1, J3.2, R1.1
unnamed: J1.1, J5.1, R6.2
unnamed: C1.1, FB1.2, R1.2, U1.3 (VIN)
unnamed: LED3.C, R5.2
unnamed: J4.3, R3.2
unnamed: LED1.A, R3.1
unnamed: LED2.A, R4.1
unnamed: J4.4, R4.2
unnamed: FB1.1, J5.2, R6.1
unnamed: J4.2, R5.1

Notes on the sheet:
Revision History
Rev
Date
Changes
2.6
26 Nov 2013
Initial Prototype
Engr
RWH
OpenROV Topside Interface Board 2.6A
Tether Connector
USB Power Connection
Header socket for Tenda V2.0 Homeplug Adapter
Power Indication
Homeplug Connect
Ethernet Connect
Notes
1.) 5V bias on tether is used to turn ROV power on 2.) Remove Resistor R1 to disable auto-power-on 3.) Remove Resistors R1 and R2 to electrically isolate tether from USB 4.) To add power switch to topside box, remove resistor R6 and connect switch across J5
Alignment Fiducials
Optional Power Switch Connector
2.6A
11 Feb 2014
No schematic changes from Rev 2.6. Positions of J1 and J2 adjusted. Longer engagement length on headers J3 and J4. Revised silkscreen and soldermask. Hole for optional standoff.

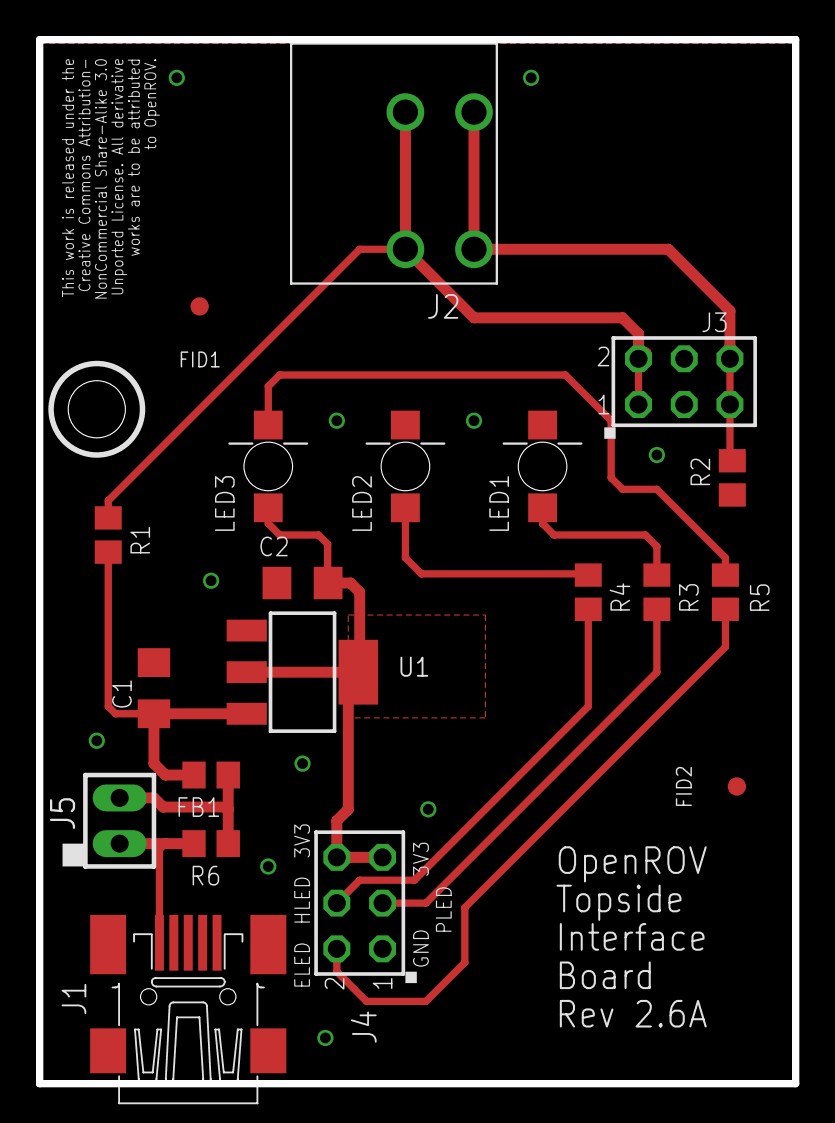
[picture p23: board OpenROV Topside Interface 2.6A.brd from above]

Board: 4 copper layers, 42.0 x 58.0 mm, 20 parts (0 on the bottom side), 13 nets.

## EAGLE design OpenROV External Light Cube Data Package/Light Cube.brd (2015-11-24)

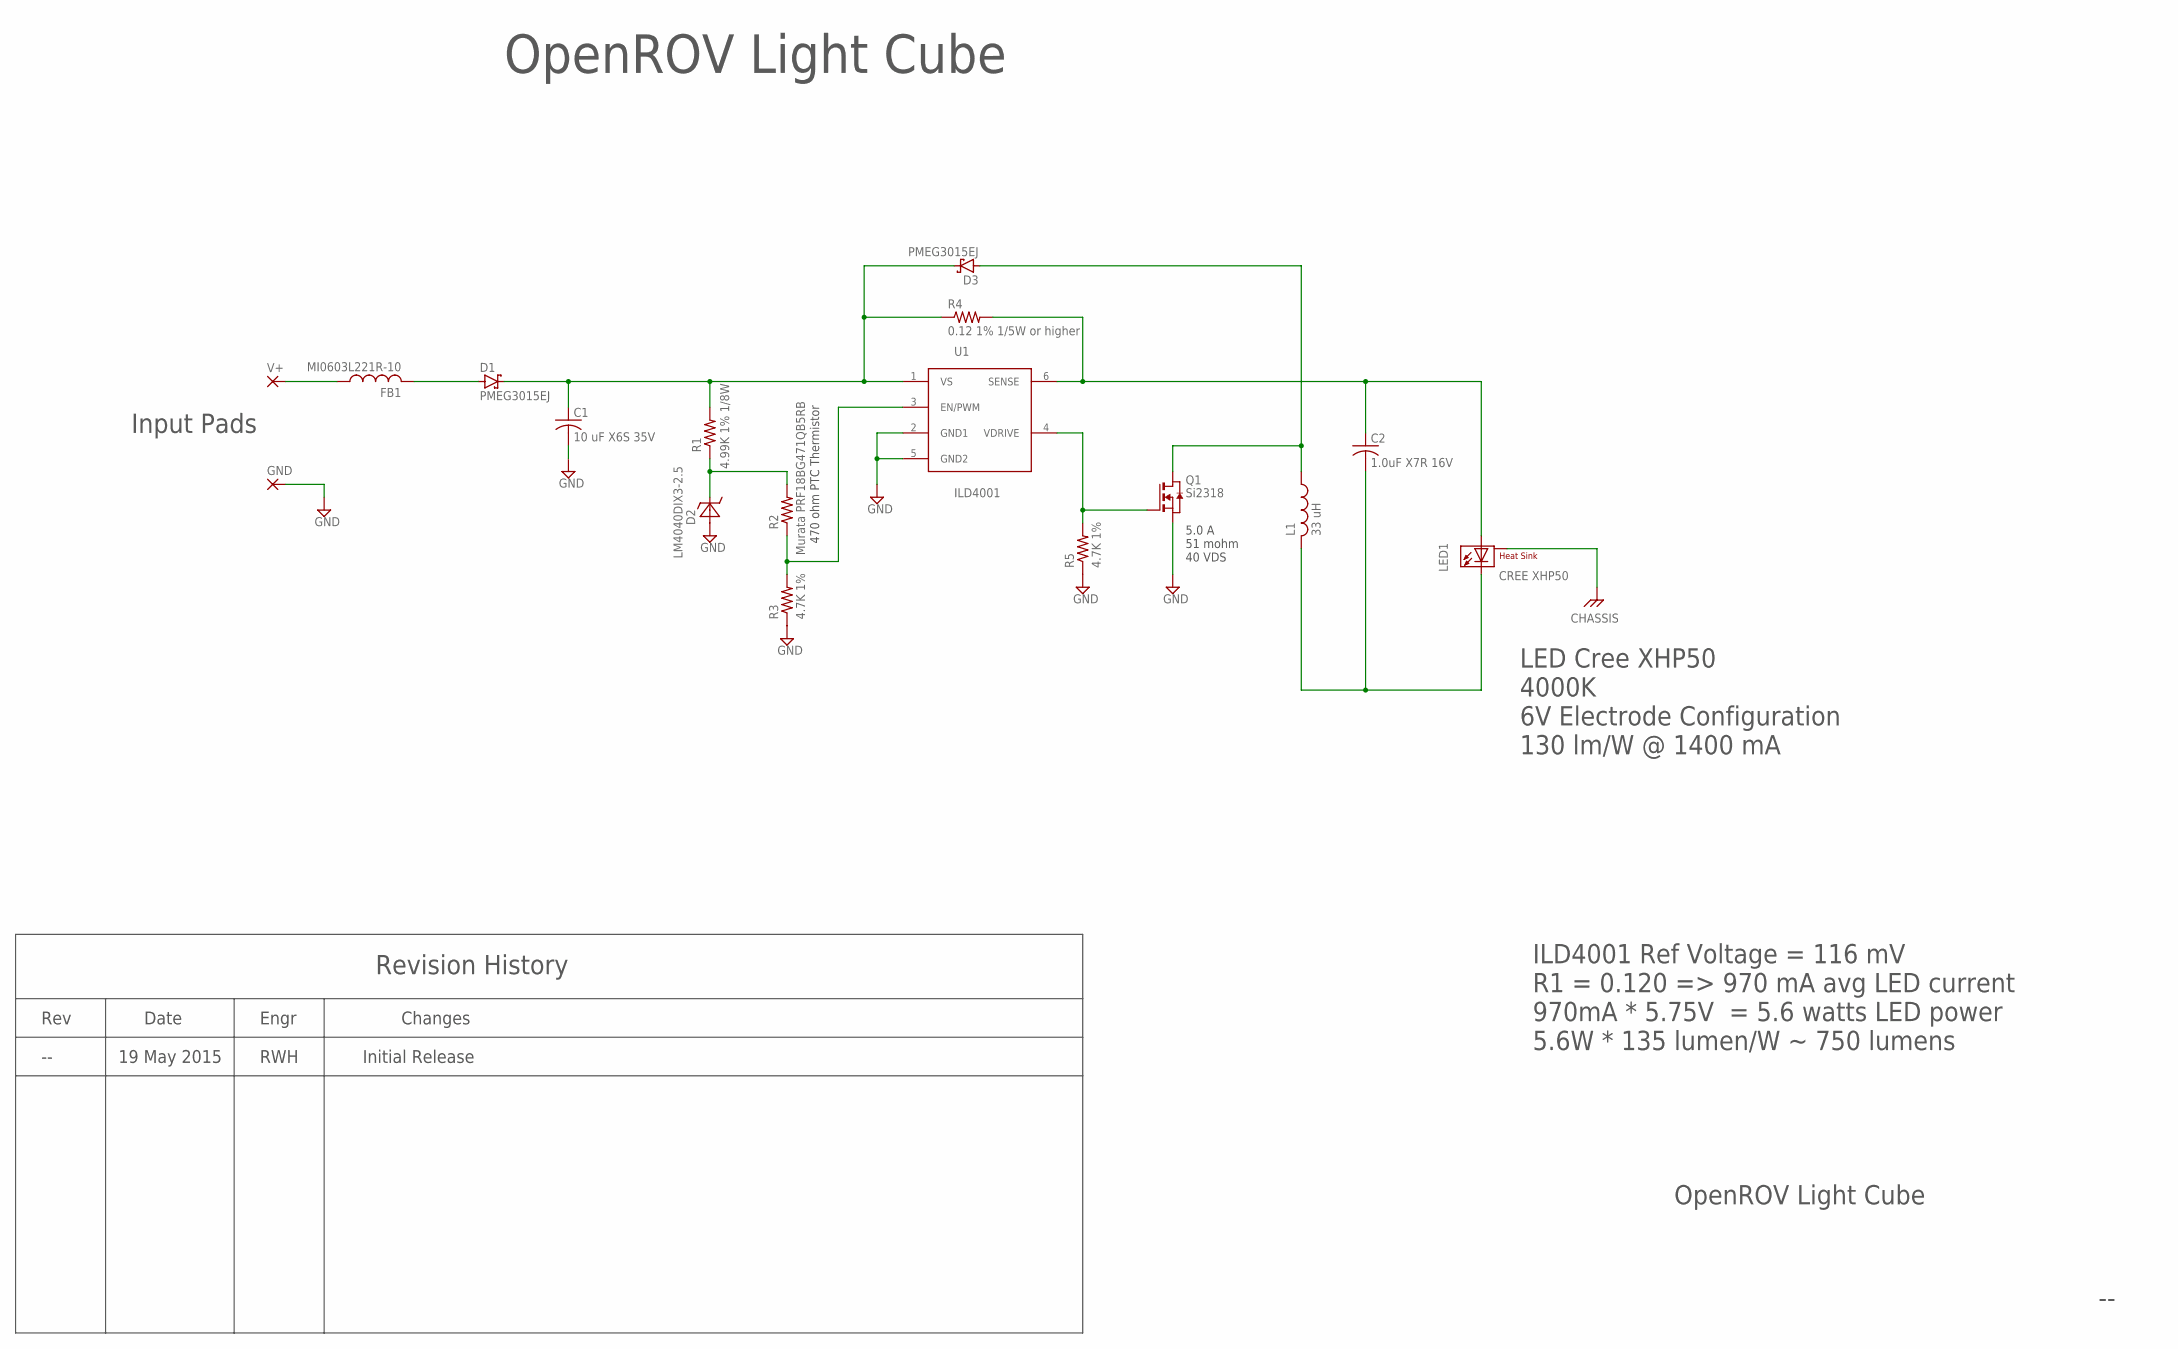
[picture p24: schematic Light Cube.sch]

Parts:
C1: 10 uF X6S 35V; R0805
C2: 1.0uF X7R 16V; R0603
D1, D3: PMEG3015EJ; SOD323
D2: LM4040DIX3-2.5; SC70-3
FB1: MI0603L221R-10; R0603
GND: SMD_PAD3/3; SMD_3_3
L1: 33 uH; INDUCTOR_LAIRD_TYS6045
LED1: CREE XHP50; CREE_XHP50_6V
Q1: Si2318; SOT23
R1: 4.99K 1% 1/8W; R0402
R2: Murata PRF18BG471QB5RB; R0603
R3, R5: 4.7K 1%; R0402
R4: 0.12 1% 1/5W or higher; R0603
U1: ILD4001; SC74_INFINEON
V+: SMD_PAD-2/2; SMD_2_2

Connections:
CHASSIS: LED1.SINK (HEATSINK)
GND: C1.2, D2.2 (A), GND.1, Q1.2 (S), R3.1, R5.1, U1.2 (GND1), U1.5 (GND2)
unnamed: D2.1 (C), R1.1, R2.2
unnamed: FB1.1, V+.1
unnamed: D1.A, FB1.2
unnamed: C1.1, D1.C, D3.C, R1.2, R4.1, U1.1 (VS)
unnamed: R2.1, R3.2, U1.3 (EN/PWM)
unnamed: C2.1, LED1.A, R4.2, U1.6 (SENSE)
unnamed: D3.A, L1.P$1 (1), Q1.3 (D)
unnamed: C2.2, L1.P$2 (2), LED1.C
unnamed: Q1.1 (G), R5.2, U1.4 (VDRIVE)

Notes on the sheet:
OpenROV Light Cube
ILD4001 Ref Voltage = 116 mV R1 = 0.120 => 970 mA avg LED current 970mA * 5.75V = 5.6 watts LED power 5.6W * 135 lumen/W ~ 750 lumens
LED Cree XHP50 4000K 6V Electrode Configuration 130 lm/W @ 1400 mA
5.0 A 51 mohm 40 VDS
Revision History
Rev
Date
Engr
Changes
19 May 2015
RWH
Initial Release
Input Pads
470 ohm PTC Thermistor

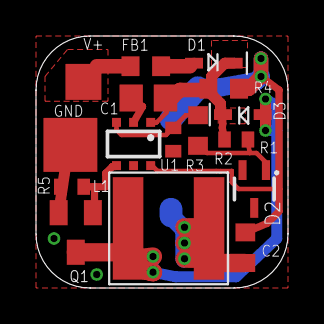
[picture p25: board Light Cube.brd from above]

Board: 4 copper layers, 14.0 x 14.0 mm, 17 parts (1 on the bottom side), 10 nets.

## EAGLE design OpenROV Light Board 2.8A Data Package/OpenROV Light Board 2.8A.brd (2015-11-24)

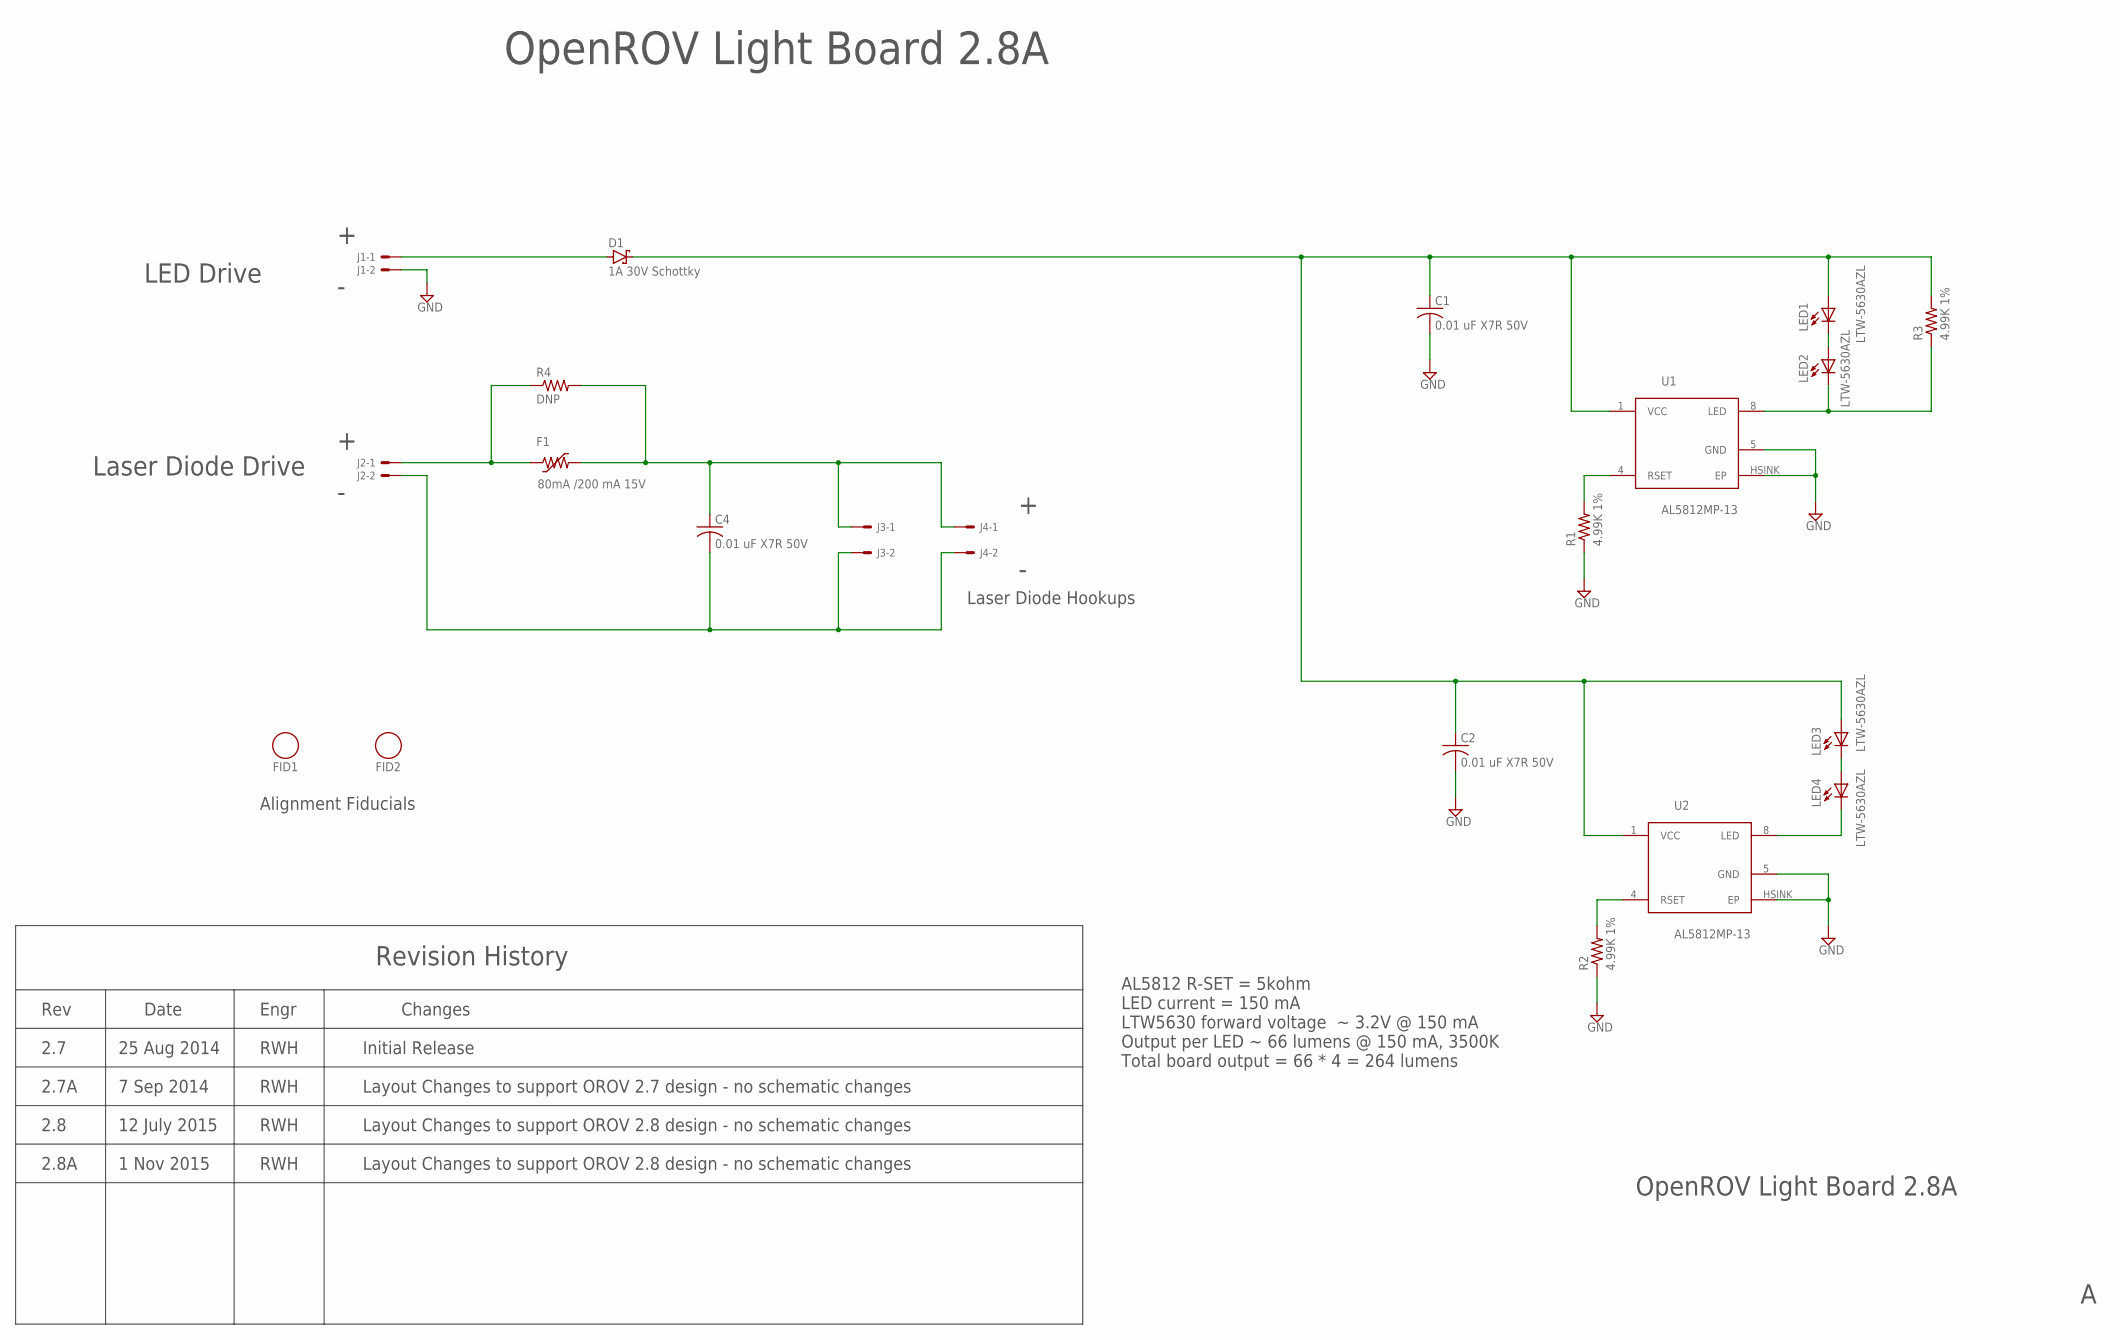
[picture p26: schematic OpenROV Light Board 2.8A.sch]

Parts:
C1, C2, C4: 0.01 uF X7R 50V; R0603
D1: 1A 30V Schottky; DO214AC
F1: 80mA /200 mA 15V; R0603
FID1, FID2: FIDUCIAL_1
J1, J2: SOLDER_PADS_3MM
J3, J4: SOLDER_PADS_3MM-SMALL_HOLE; SOLDER_PADS_3MM_SMALL_HOLE
LED1, LED2, LED3, LED4: LTW-5630AZL; LITEON-5630
R1, R2, R3: 4.99K 1%; R0603
R4: DNP; R1206
U1, U2: AL5812MP-13; MSOP-8EP

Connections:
GND: C1.2, C2.2, J1.2, R1.1, R2.1, U1.5 (GND), U1.HSINK (EP), U2.5 (GND), U2.HSINK (EP)
unnamed: LED2.C1 (C), LED2.C2 (C), R3.1, U1.8 (LED)
unnamed: LED1.C1 (C), LED1.C2 (C), LED2.A1 (A), LED2.A2 (A), LED2.A3 (A)
unnamed: C4.1, F1.2, J3.1, J4.1, R4.2
unnamed: C4.2, J2.2, J3.2, J4.2
unnamed: F1.1, J2.1, R4.1
unnamed: R1.2, U1.4 (RSET)
unnamed: LED4.C1 (C), LED4.C2 (C), U2.8 (LED)
unnamed: LED3.C1 (C), LED3.C2 (C), LED4.A1 (A), LED4.A2 (A), LED4.A3 (A)
unnamed: C1.1, C2.1, D1.C, LED1.A1 (A), LED1.A2 (A), LED1.A3 (A), LED3.A1 (A), LED3.A2 (A), LED3.A3 (A), R3.2, U1.1 (VCC), U2.1 (VCC)
unnamed: D1.A, J1.1
unnamed: R2.2, U2.4 (RSET)

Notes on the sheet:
OpenROV Light Board 2.8A
Laser Diode Drive
LED Drive
Laser Diode Hookups
Revision History
Rev
Date
Engr
Changes
2.7
25 Aug 2014
RWH
Initial Release
Alignment Fiducials
Layout Changes to support OROV 2.7 design - no schematic changes
7 Sep 2014
2.7A
2.8
12 July 2015
Layout Changes to support OROV 2.8 design - no schematic changes
AL5812 R-SET = 5kohm LED current = 150 mA LTW5630 forward voltage ~ 3.2V @ 150 mA Output per LED ~ 66 lumens @ 150 mA, 3500K Total board output = 66 * 4 = 264 lumens
2.8A
1 Nov 2015

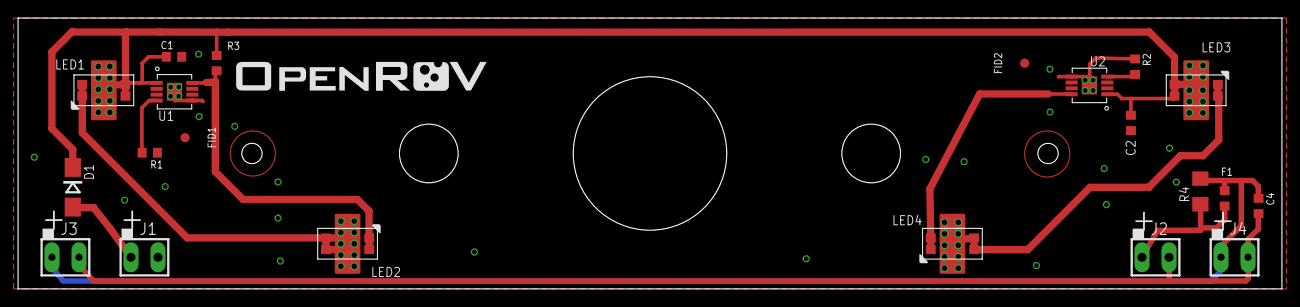
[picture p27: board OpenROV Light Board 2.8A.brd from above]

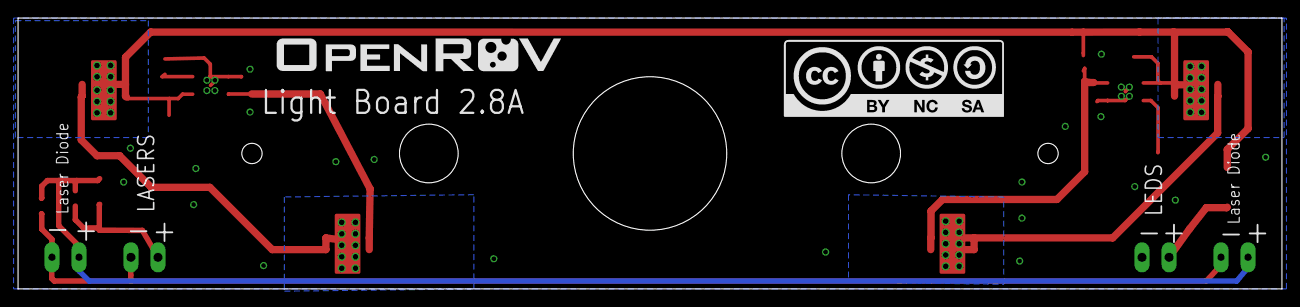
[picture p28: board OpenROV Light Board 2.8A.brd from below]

Board: 4 copper layers, 140.0 x 30.0 mm, 24 parts (2 on the bottom side), 12 nets.

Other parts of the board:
U$1: CC-LOGO-1-TOP
U$2: OROV-LOGO-1.25
U$4: OROV-LOGO-1.10

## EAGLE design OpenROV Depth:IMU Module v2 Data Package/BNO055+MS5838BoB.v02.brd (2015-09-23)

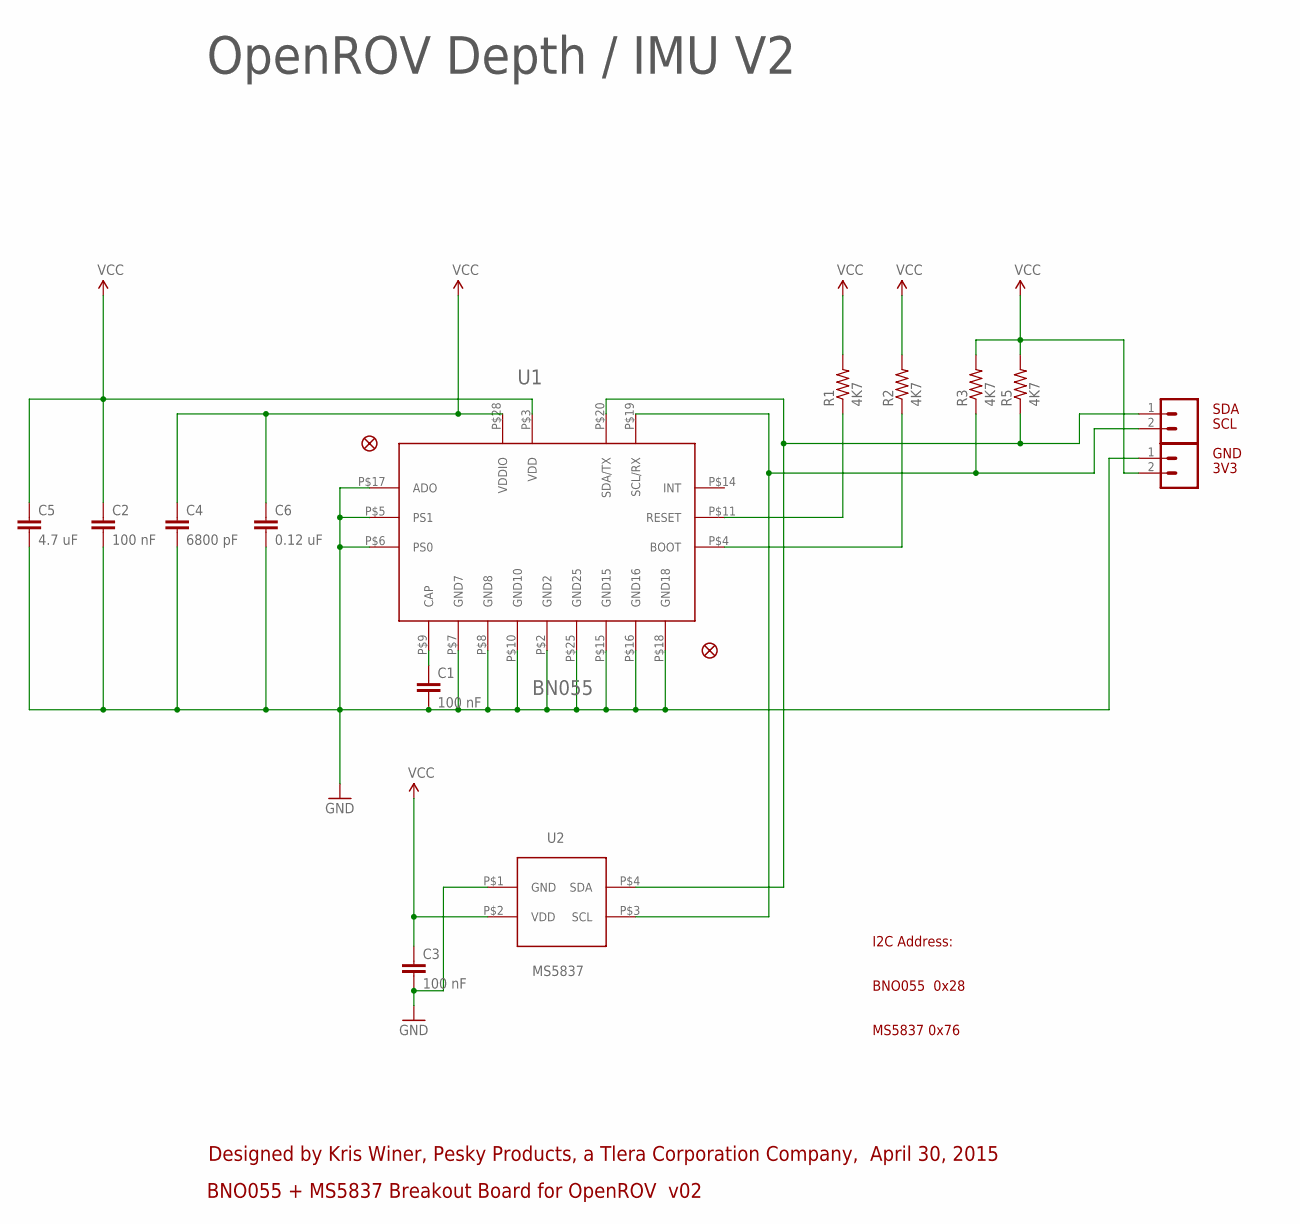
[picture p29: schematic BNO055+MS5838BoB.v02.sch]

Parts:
C1, C2, C3: 100 nF; C0402
C4: 6800 pF; C0402
C5: 4.7 uF; C0402
C6: 0.12 uF; C0402
FID1, FID2: FIDUCIALUFIDUCIAL; MICRO-FIDUCIAL
JP2, JP3: M021X02_NO_SILK; 1X02_NO_SILK
R1, R2, R3, R5: 4K7; R0402
U1: BN055; LGA28
U2: MS5837

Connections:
GND: C1.2, C2.2, C3.2, C4.2, C5.2, C6.2, JP3.1, U1.P$2 (GND2), U1.P$5 (PS1), U1.P$6 (PS0), U1.P$7 (GND7), U1.P$8 (GND8), U1.P$10 (GND10), U1.P$15 (GND15), U1.P$16 (GND16), U1.P$17 (ADO), U1.P$18 (GND18), U1.P$25 (GND25), U2.P$1 (GND)
unnamed: R1.1, U1.P$11 (RESET)
unnamed: C1.1, U1.P$9 (CAP)
unnamed: R2.1, U1.P$4 (BOOT)
SCL: JP2.2, R3.1, U1.P$19 (SCL/RX), U2.P$3 (SCL)
SDA: JP2.1, R5.1, U1.P$20 (SDA/TX), U2.P$4 (SDA)
VCC: C2.1, C3.1, C4.1, C5.1, C6.1, JP3.2, R1.2, R2.2, R3.2, R5.2, U1.P$3 (VDD), U1.P$28 (VDDIO), U2.P$2 (VDD)

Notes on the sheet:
Designed by Kris Winer, Pesky Products, a Tlera Corporation Company, April 30, 2015
BNO055 + MS5837 Breakout Board for OpenROV v02
SDA
SCL
GND
3V3
I2C Address:
BNO055 0x28
MS5837 0x76
OpenROV Depth / IMU V2

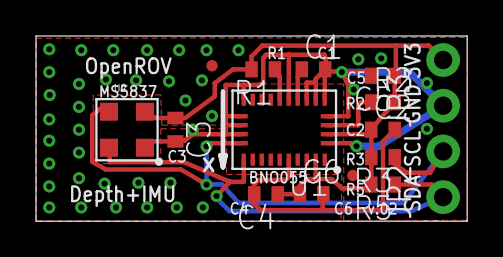
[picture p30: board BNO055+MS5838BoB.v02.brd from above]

Board: 2 copper layers, 24.0 x 10.3 mm, 17 parts (1 on the bottom side), 7 nets.

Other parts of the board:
U$2: OROV-LOGO-0.500

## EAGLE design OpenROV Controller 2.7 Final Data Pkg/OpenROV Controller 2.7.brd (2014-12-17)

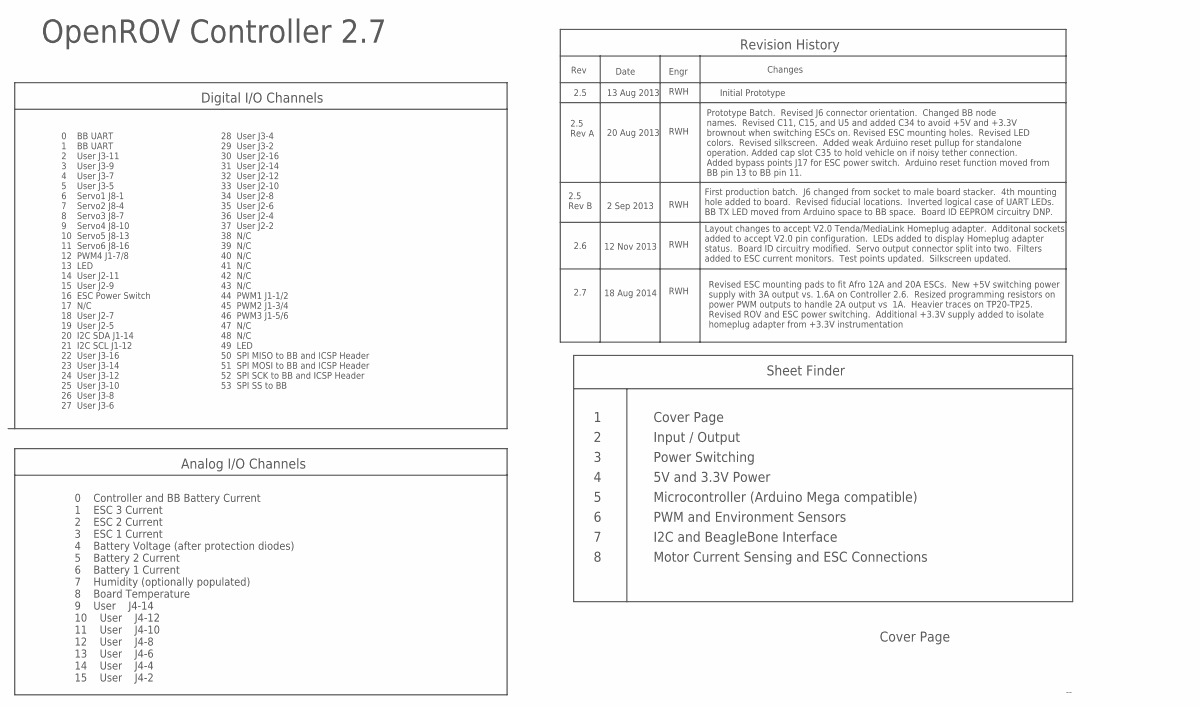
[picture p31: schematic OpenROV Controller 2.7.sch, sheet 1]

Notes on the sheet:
Revision History
Rev
Date
Changes
2.5
13 Aug 2013
Initial Prototype
Sheet Finder
Cover Page
Input / Output
Power Switching
5V and 3.3V Power
Microcontroller (Arduino Mega compatible)
PWM and Environment Sensors
I2C and BeagleBone Interface
OpenROV Controller 2.7
Analog I/O Channels
Digital I/O Channels
Motor Current Sensing and ESC Connections
0 Controller and BB Battery Current 1 ESC 3 Current 2 ESC 2 Current 3 ESC 1 Current 4 Battery Voltage (after protection diodes) 5 Battery 2 Current 6 Battery 1 Current 7 Humidity (optionally populated) 8 Board Temperature 9 User J4-14 10 User J4-12 11 User J4-10 12 User J4-8 13 User J4-6 14 User J4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
0 BB UART 1 BB UART 2 User J3-11 3 User J3-9 4 User J3-7 5 User J3-5 6 Servo1 J8-1 7 Servo2 J8-4 8 Servo3 J8-7 9 Servo4 J8-10 10 Servo5 J8-13 11 Servo6 J8-16 12 PWM4 J1-7/8 13 LED 14 User J2-11 15 User J2-9 16 ESC Power Switch 17 N/C 18 User J2-7 19 User J2-5 20 I2C SDA J1-14 21 I2C SCL J1-12 22 Us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
Engr
RWH
28 User J3-4 29 User J3-2 30 User J2-16 31 User J2-14 32 User J2-12 33 User J2-10 34 User J2-8 35 User J2-6 36 User J2-4 37 User J2-2 38 N/C 39 N/C 40 N/C 41 N/C 42 N/C 43 N/C 44 PWM1 J1-1/2 45 PWM2 J1-3/4 46 PWM3 J1-5/6 47 N/C 48 N/C 49 LED 50 SPI MISO to BB and ICSP Header 51 SPI MOSI to BB and I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
2.5 Rev A
20 Aug 2013
Prototype Batch. Revised J6 connector orientation. Changed BB node names. Revised C11, C15, and U5 and added C34 to avoid +5V and +3.3V brownout when switching ESCs on. Revised ESC mounting holes. Revised LED colors. Revised silkscreen. Added weak Arduino reset pullup for standalone operation. Adde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
2.5 Rev B
2 Sep 2013
First production batch. J6 changed from socket to male board stacker. 4th mounting hole added to board. Revised fiducial locations. Inverted logical case of UART LEDs. BB TX LED moved from Arduino space to BB space. Board ID EEPROM circuitry DNP.
2.6
12 Nov 2013
Layout changes to accept V2.0 Tenda/MediaLink Homeplug adapter. Additonal sockets added to accept V2.0 pin configuration. LEDs added to display Homeplug adapter status. Board ID circuitry modified. Servo output connector split into two. Filters added to ESC current monitors. Test points updated. Si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
2.7
18 Aug 2014
Revised ESC mounting pads to fit Afro 12A and 20A ESCs. New +5V switching power supply with 3A output vs. 1.6A on Controller 2.6. Resized programming resistors on power PWM outputs to handle 2A output vs 1A. Heavier traces on TP20-TP25. Revised ROV and ESC power switching. Additional +3.3V supply a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

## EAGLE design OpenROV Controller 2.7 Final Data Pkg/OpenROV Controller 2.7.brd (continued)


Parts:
FID1, FID2, FID3, FID4, FID5: FIDUCIAL_1
J1, J2, J3, J4: SSW-108-01-G-D; SSW-108-02-S-D
J5: FCI 10090096-P254; M25VP
J6: Samtec DW-23-11-G-D-630; TSW-123-02-S-D
J7: HDR_1X2X0.100-ALT_SILK; 22-23-2021_ALT_SILK
J9, J10: HDR_1X3X0.100-ALT_SILK; 22-23-2031_ALT_SILK
J18, J19: Sullins PRPC003DFAN-RC; SSW-103-02-S-D
J20, J21: TSW-103-07-G-T; HDR_PINS_3X3
LED6: GREEN; LED_CHIPLED_0603
LED7, LED8: YELLOW; LED_CHIPLED_0603
R63, R64: 120; R0603
R65: 330; R0603
TP2, TP3, TP20, TP21, TP22, TP23, TP24, TP25: TEST_PAD-1.0; 2.0/1.0

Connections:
3V3_SCL: J1.11, J5.15; also elsewhere on the board
3V3_SDA: J1.13, J5.16; also elsewhere on the board
+3V3: J1.9, J4.13, J5.14; also elsewhere on the board
+3V3_HOMEPLUG: J9.2, J18.5, J18.6, LED8.A; also elsewhere on the board
+5V: J1.10, J2.1, J2.15, J3.1, J3.15, J4.15, J6.5, J6.6; also elsewhere on the board
ADC9: J4.14; also elsewhere on the board
ADC10: J4.12; also elsewhere on the board
ADC11: J4.10; also elsewhere on the board
ADC12: J4.8; also elsewhere on the board
ADC13: J4.6; also elsewhere on the board
ADC14: J4.4; also elsewhere on the board
ADC15: J4.2; also elsewhere on the board
AREF: J4.16; also elsewhere on the board
BAT_1+: J5.5; also elsewhere on the board
BAT_2+: J5.6; also elsewhere on the board
BB_3V3: J6.3, J6.4; also elsewhere on the board
BB_P9_11: J6.11; also elsewhere on the board
BB_P9_12: J6.12
BB_P9_13: J6.13
BB_P9_14: J6.14
BB_P9_15: J6.15
BB_P9_16: J6.16
BB_P9_17: J6.17; also elsewhere on the board
BB_P9_18: J6.18; also elsewhere on the board
BB_P9_19: J6.19; also elsewhere on the board
BB_P9_20: J6.20; also elsewhere on the board
BB_P9_21: J6.21; also elsewhere on the board
BB_P9_22: J6.22; also elsewhere on the board
BB_P9_23: J6.23
BB_P9_24: J6.24; also elsewhere on the board
BB_P9_25: J6.25
BB_P9_26: J6.26; also elsewhere on the board
BB_P9_27: J6.27
BB_P9_28: J6.28
BB_P9_29: J6.29
BB_P9_30: J6.30
BB_P9_31: J6.31
BB_P9_32: J6.32
BB_P9_33: J6.33
BB_P9_34: J6.34
BB_P9_35: J6.35
BB_P9_36: J6.36
BB_P9_37: J6.37
BB_P9_38: J6.38
BB_P9_39: J6.39
BB_P9_40: J6.40
BB_P9_41: J6.41
BB_P9_42: J6.42
BB_PWR_BUT: J6.9
BB_SYS_5V: J6.7, J6.8
BB_SYS_RESET*: J6.10; also elsewhere on the board
D2: J3.11; also elsewhere on the board
D3: J3.9; also elsewhere on the board
D4: J3.7; also elsewhere on the board
D5: J3.5; also elsewhere on the board
D6: J20.P1; also elsewhere on the board
D7: J20.P4; also elsewhere on the board
D8: J20.P7; also elsewhere on the board
D9: J21.P1; also elsewhere on the board
D10: J21.P4; also elsewhere on the board
D11: J21.P7; also elsewhere on the board
D14: J2.11; also elsewhere on the board
D15: J2.9; also elsewhere on the board
D18: J2.7; also elsewhere on the board
D19: J2.5; also elsewhere on the board
D20/5V_SDA: J1.14; also elsewhere on the board
D21/5V_SCL: J1.12; also elsewhere on the board
D22: J3.16; also elsewhere on the board
D23: J3.14; also elsewhere on the board
D24: J3.12; also elsewhere on the board
D25: J3.10; also elsewhere on the board
D26: J3.8; also elsewhere on the board
D27: J3.6; also elsewhere on the board
D28: J3.4; also elsewhere on the board
D29: J3.2; also elsewhere on the board
D30: J2.16; also elsewhere on the board
D31: J2.14; also elsewhere on the board
D32: J2.12; also elsewhere on the board
D33: J2.10; also elsewhere on the board
D34: J2.8; also elsewhere on the board
D35: J2.6; also elsewhere on the board
D36: J2.4; also elsewhere on the board
D37: J2.2; also elsewhere on the board
ESC_1A: J5.1; also elsewhere on the board
ESC_1B: J5.2; also elsewhere on the board
ESC_1C: J5.3; also elsewhere on the board
ESC_2A: J5.8; also elsewhere on the board
ESC_2B: J5.9; also elsewhere on the board
ESC_2C: J5.10; also elsewhere on the board
ESC_3A: J5.11; also elsewhere on the board
ESC_3B: J5.12; also elsewhere on the board
ESC_3C: J5.13; also elsewhere on the board
GND: J1.15, J1.16, J2.3, J2.13, J3.3, J3.13, J4.1, J4.3, J4.5, J4.7, J4.9, J4.11, J5.4, J5.7, J5.17, J6.1, J6.2, J6.43, J6.44, J6.45, J6.46, J7.2, J9.1, J9.3, J18.1, J20.P3, J20.P6, J20.P9, J21.P3, J21.P6, J21.P9, LED6.C, LED7.C, TP2.1, TP3.1; also elsewhere on the board
unnamed: LED6.A, R63.1
unnamed: J5.24, TP24.1
unnamed: J5.20, TP20.1
unnamed: J7.1, J20.P2, J20.P5, J20.P8, J21.P2, J21.P5, J21.P8
unnamed: J5.21, TP21.1
unnamed: J5.22, TP22.1
unnamed: J5.23, TP23.1
unnamed: J5.25, TP25.1
unnamed: J18.3, R63.2
unnamed: J18.4, R64.2
unnamed: LED7.A, R64.1
unnamed: J18.2, R65.2
unnamed: LED8.C, R65.1
PWM_1+: J1.1; also elsewhere on the board
PWM_1-: J1.2; also elsewhere on the board
PWM_2+: J1.3; also elsewhere on the board
PWM_2-: J1.4; also elsewhere on the board
PWM_3+: J1.5; also elsewhere on the board
PWM_3-: J1.6; also elsewhere on the board
PWM_4+: J1.7; also elsewhere on the board
PWM_4-: J1.8; also elsewhere on the board
TETHER_A: J5.18, J10.1, J19.1, J19.2; also elsewhere on the board
TETHER_B: J5.19, J10.3, J19.5, J19.6; also elsewhere on the board

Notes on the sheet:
Input / Output
Servo Outputs
Wire Harness Connector
DB-25 Male Vertical Connector
Header Sockets
BeagleBone P9 Connector
Homeplug Adapter Connectors
Servo1
Servo2
Servo3
Servo4
Servo5
Servo6
External Servo Power (BEC)
This ground pin is not connected to the ground plane, but is run back to connector J1
Alignment Fiducials
Header Pins for Tenda V2.0 Adapters 0.32" Engagement Length
Solder Pads for Tenda V1.0 Adapters
Ground Points
HomePlug Ethernet
HomePlug Connect
HomePlug Adapter Power


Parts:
C1, C2, C3, C4, C5, C6, C7: 0.1 uF; R0603
C35: 10 uF 25V X5R; R0805
C42: 1 uF 25V X7R; R0603
D1, D2: MBRD835L; DPAK
D3: SMAJ18A; DO214AC
D4, D5: 16.18V 2%; SOD323
FB1: HZ0805B272R-10; R0805
J11, J12, J17: HDR_1X2X0.100-ALT_SILK; 22-23-2021_ALT_SILK
OC1: LTV-8141S; DIL4-SMD
Q1: SI4485; SO8
Q2: DMN65D8L; SOT23
Q3: SI4459ADY; SO8
R1, R2: 0.005 1%; R1206
R3: 18K; R0603
R4, R6, R7: 10K; R0603
R5, R8, R9: 1K; R0603
R10: 30.1K 1%; R0603
R11: 10.0K 1%; R0603
R12: 0.025 1%; R0805
U1, U2, U3: INA199A2; SC70-6L

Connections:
+5V: C3.1, C4.1, C7.1, U1.3 (V+), U2.3 (V+), U3.3 (V+); also elsewhere on the board
ADC0: U3.6 (VOUT); also elsewhere on the board
ADC4: C6.1, R10.2, R11.1; also elsewhere on the board
ADC5: U1.6 (VOUT); also elsewhere on the board
ADC6: U2.6 (VOUT); also elsewhere on the board
BAT_1+: C1.1, D1.1 (A), D1.3 (A); also elsewhere on the board
BAT_1-1: Q1.5 (D), Q1.6 (D), Q1.7 (D), Q1.8 (D), R10.1, R12.1, U3.4 (IN+)
BAT_2+: C2.1, D2.1 (A), D2.3 (A); also elsewhere on the board
D16/ESC_POWER_SWITCH: R5.2; also elsewhere on the board
ESC_POWER: Q3.5 (D), Q3.6 (D), Q3.7 (D), Q3.8 (D); also elsewhere on the board
GND: C1.2, C2.2, C3.2, C4.2, C6.2, C7.2, C35.2, D3.A, J11.2, J12.2, J17.2, OC1.3 (E), Q2.2 (S), R7.2, R11.2, U1.1 (REF), U1.2 (GND), U2.1 (REF), U2.2 (GND), U3.1 (REF), U3.2 (GND); also elsewhere on the board
unnamed: OC1.1 (IN-A), R3.1
unnamed: C42.2, D5.A, Q3.4 (G), R6.1, R9.2
unnamed: J17.1, Q2.3 (D), R9.1
unnamed: D1.4 (C), R1.1, U2.4 (IN+)
unnamed: Q2.1 (G), R5.1, R7.1
unnamed: C42.1, D3.C, D4.C, D5.C, J11.1, Q1.1 (S), Q1.2 (S), Q1.3 (S), Q3.1 (S), Q3.2 (S), Q3.3 (S), R1.2, R2.2, R4.2, R6.2, U1.5 (IN-), U2.5 (IN-)
unnamed: D4.A, Q1.4 (G), R4.1, R8.2
unnamed: C5.1, FB1.2, R3.2
unnamed: D2.4 (C), R2.1, U1.4 (IN+)
unnamed: C35.1, J12.1, OC1.4 (C), R8.1
TETHER_A: FB1.1; also elsewhere on the board
TETHER_B: C5.2, OC1.2 (IN-B); also elsewhere on the board
V_BAT: R12.2, U3.5 (IN-); also elsewhere on the board

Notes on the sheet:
Power Switching
30V 42 mohm 6A
30V 29A 5 mohm
1206 3/4W or higher
Battery 1 Current 10A Full-Scale Range into 5V A/D
Battery 2 Current 10A Full-Scale Range into 5V A/D
Non-ESC Current 2A Full-Scale Range into 5V A/D
Power Switch
Aux Power Input
Battery Voltage (measured after protection diodes) +20V full-scale into 5V A/D
ESC Power Switch


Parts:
C8, C9, C16: 10 uF 25V X5R; R0805
C10, C11: 3900 pF 25V NP0; R0603
C12, C15, C43: 0.1 uF; R0603
C13, C14: 22 uF 10V X5R; R0805
C34: 220 uF 10V; NICHICON_8MM
C44: 1 uF 25V X7R; R0603
D6: SMAJ15A; DO214AC
F1: 2.0A / 4.0A 24V; R2920
L1: 15 uH 4A; INDUCTOR_BOURNS_12X0
LED1: GREEN; LED_CHIPLED_0603
R13: 100K; R0603
R14: 13.0K 1%; R0603
R16: 45.3K 1%; R0603
R17: 10.0K 1%; R0603
R18: 1K; R0603
U4: Richtek RT8250; SO8-THERMAL
U5: TLV1117LV33DCY; SOT223
U12: TCR2EF33; SOT23-5L

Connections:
+3V3: C44.1, U12.5 (VOUT); also elsewhere on the board
+3V3_HOMEPLUG: C16.1, U5.2 (VOUT), U5.4 (VOUT); also elsewhere on the board
+5V: C13.1, C14.1, C15.1, C34.+, C43.1, L1.2, R16.2, R18.1, U5.3 (VIN), U12.1 (VIN), U12.3 (CTRL); also elsewhere on the board
FUSED_VBAT: C8.1, C9.1, D6.C, F1.2, R13.1, U4.2 (VIN)
GND: C8.2, C9.2, C11.2, C13.2, C14.2, C15.2, C16.2, C34.-, C43.2, C44.2, D6.A, LED1.C, R14.1, R17.1, U4.4 (GND), U4.PAD (GNDPAD), U5.1 (GND), U12.2 (GND); also elsewhere on the board
unnamed: LED1.A, R18.2
unnamed: R16.1, R17.2, U4.5 (FB)
unnamed: R13.2, U4.7 (EN)
unnamed: C11.1, U4.8 (SS)
unnamed: C12.1, U4.1 (BOOT)
unnamed: C12.2, L1.1, U4.3 (SW)
unnamed: C10.1, U4.6 (COMP)
unnamed: C10.2, R14.2
V_BAT: F1.1; also elsewhere on the board

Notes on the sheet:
5V and 3.3V Power
5V Power LED


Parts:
C17, C18, C21, C22, C23: 0.1 uF; R0603
C19, C20: 12 pF; R0603
LED2, LED5: RED; LED_CHIPLED_0603
LED4: YELLOW; LED_CHIPLED_0603
R19, R22, R23: 1K; R0603
R20: 100K; R0603
U6: ATMEGA2560-16AU; SMARTPRJ_TQFP100
X1: 16 MHz; DISCRETE_2P-SMD-5X3.2

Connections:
+5V: C17.1, C18.1, C22.1, C23.1, LED4.A, R20.1, U6.10 (VCC), U6.31 (VCC1), U6.61 (VCC2), U6.80 (VCC3), U6.100 (AVCC); also elsewhere on the board
ADC0: U6.97 ((ADC0)PF0); also elsewhere on the board
ADC1: U6.96 ((ADC1)PF1); also elsewhere on the board
ADC2: U6.95 ((ADC2)PF2); also elsewhere on the board
ADC3: U6.94 ((ADC3)PF3); also elsewhere on the board
ADC4: U6.93 ((ADC4/TCK)PF4); also elsewhere on the board
ADC5: U6.92 ((ADC5/TMS)PF5); also elsewhere on the board
ADC6: U6.91 ((ADC6/TDO)PF6); also elsewhere on the board
ADC7: U6.90 ((ADC7/TDI)PF7); also elsewhere on the board
ADC8: U6.89 (PK0(ADC8/PCINT16)); also elsewhere on the board
ADC9: U6.88 (PK1(ADC9/PCINT17)); also elsewhere on the board
ADC10: U6.87 (PK2(ADC10/PCINT18)); also elsewhere on the board
ADC11: U6.86 (PK3(ADC11/PCINT19)); also elsewhere on the board
ADC12: U6.85 (PK4(ADC12/PCINT20)); also elsewhere on the board
ADC13: U6.84 (PK5(ADC13/PCINT21)); also elsewhere on the board
ADC14: U6.83 (PK6(ADC14/PCINT22)); also elsewhere on the board
ADC15: U6.82 (PK7(ADC15/PCINT23)); also elsewhere on the board
AREF: C21.1, U6.98 (AREF); also elsewhere on the board
D0/UART_RX: U6.2 ((RXD0/PCIN8)PE0); also elsewhere on the board
D1/UART_TX: R22.2, U6.3 ((TXD0)PE1); also elsewhere on the board
D2: U6.6 ((OC3B/INT4)PE4); also elsewhere on the board
D3: U6.7 ((OC3C/INT5)PE5); also elsewhere on the board
D4: U6.1 ((OC0B)PG5); also elsewhere on the board
D5: U6.5 ((OC3A/AIN1)PE3); also elsewhere on the board
D6: U6.15 (PH3(OC4A)); also elsewhere on the board
D7: U6.16 (PH4(OC4B)); also elsewhere on the board
D8: U6.17 (PH5(OC4C)); also elsewhere on the board
D9: U6.18 (PH6(OC2B)); also elsewhere on the board
D10: U6.23 ((OC2A/PCINT4)PB4); also elsewhere on the board
D11: U6.24 ((OC1A/PCINT5)PB5); also elsewhere on the board
D12: U6.25 ((OC1B/PCINT6)PB6); also elsewhere on the board
D13: R23.1, U6.26 ((OC0A/OC1C/PCINT7)PB7)
D14: U6.64 (PJ1(TXD3/PCINT10)); also elsewhere on the board
D15: U6.63 (PJ0(RXD3/PCINT9)); also elsewhere on the board
D16/ESC_POWER_SWITCH: U6.13 (PH1(TXD2)); also elsewhere on the board
D17: U6.12 (PH0(RXD2))
D18: U6.46 ((TXD1/INT3)PD3); also elsewhere on the board
D19: U6.45 ((RXD1/INT2)PD2); also elsewhere on the board
D20/5V_SDA: U6.44 ((SDA/INT1)PD1); also elsewhere on the board
D21/5V_SCL: U6.43 ((SCL/INT0)PD0); also elsewhere on the board
D22: U6.78 ((AD0)PA0); also elsewhere on the board
D23: U6.77 ((AD1)PA1); also elsewhere on the board
D24: U6.76 ((AD2)PA2); also elsewhere on the board
D25: U6.75 ((AD3)PA3); also elsewhere on the board
D26: U6.74 ((AD4)PA4); also elsewhere on the board
D27: U6.73 ((AD5)PA5); also elsewhere on the board
D28: U6.72 ((AD6)PA6); also elsewhere on the board
D29: U6.71 ((AD7)PA7); also elsewhere on the board
D30: U6.60 ((A15)PC7); also elsewhere on the board
D31: U6.59 ((A14)PC6); also elsewhere on the board
D32: U6.58 ((A13)PC5); also elsewhere on the board
D33: U6.57 ((A12)PC4); also elsewhere on the board
D34: U6.56 ((A11)PC3); also elsewhere on the board
D35: U6.55 ((A10)PC2); also elsewhere on the board
D36: U6.54 ((A9)PC1); also elsewhere on the board
D37: U6.53 ((A8)PC0); also elsewhere on the board
D38: U6.50 ((T0)PD7)
D39: U6.70 ((ALE)PG2)
D40: U6.52 ((RD)PG1)
D41: U6.51 ((WR)PG0)
D42: U6.42 (PL7)
D43: U6.41 (PL6)
D44: U6.40 (PL5(OC5C)); also elsewhere on the board
D45: U6.39 (PL4(OC5B)); also elsewhere on the board
D46: U6.38 (PL3(OC5A)); also elsewhere on the board
D47: U6.37 (PL2(T5))
D48: U6.36 (PL1(ICP5))
D49: R19.1, U6.35 (PL0(ICP4))
D50/SPI_MISO: U6.22 ((MISO/PCINT3)PB3); also elsewhere on the board
D51/SPI_MOSI: U6.21 ((MOSI/PCINT2)PB2); also elsewhere on the board
D52/SPI_SCK: U6.20 ((SCK/PCINT1)PB1); also elsewhere on the board
D53/SPI_SS: U6.19 ((SS/PCINT0)PB0); also elsewhere on the board
GND: C17.2, C18.2, C19.2, C20.2, C21.2, C22.2, C23.2, LED2.C, LED5.C, U6.11 (GND), U6.32 (GND1), U6.62 (GND2), U6.81 (GND3), U6.99 (AGND); also elsewhere on the board
unnamed: LED2.A, R19.2
unnamed: C19.1, U6.33 (XTAL2), X1.2
unnamed: C20.1, U6.34 (XTAL1), X1.1
unnamed: LED5.A, R23.2
unnamed: LED4.C, R22.1
RESET_N: R20.2, U6.30 (RESET); also elsewhere on the board

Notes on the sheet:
Microcontroller
Adapted from Arduino Mega 2560 R3
D13 LED
D49 LED
BB RX LED


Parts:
C24, C25, C26, C27: 0.1 uF; R0603
D7, D8, D9, D10: S1A; DO214AC
Q4, Q5, Q6, Q7: IRLML6346TR; SOT23
R24, R25, R27, R29, R30, R31, R32, R33, R34, R35: DNP; R0805
R26, R28: 0 (Jumper); R0805
R36, R37, R38, R39: 1K; R0603
R40, R41, R42, R43, R44, R45: 10K; R0603
SENS1: HIH-5031
SENS2: MCP9701A; SOT23

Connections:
+3V3: R24.1, R27.1, R30.1, R33.1; also elsewhere on the board
+5V: C24.1, C25.1, R25.1, R28.1, R31.1, R34.1, SENS1.3 (V+), SENS2.1 (VDD); also elsewhere on the board
ADC7: C27.1, R45.2; also elsewhere on the board
ADC8: C26.1, R44.2; also elsewhere on the board
D12: R39.1; also elsewhere on the board
D44: R36.1; also elsewhere on the board
D45: R37.1; also elsewhere on the board
D46: R38.1; also elsewhere on the board
GND: C24.2, C25.2, C26.2, C27.2, Q4.2 (S), Q5.2 (S), Q6.2 (S), Q7.2 (S), R40.1, R41.1, R42.1, R43.1, SENS1.1 (GND), SENS1.PAD, SENS2.3 (GND); also elsewhere on the board
unnamed: R45.1, SENS1.2 (OUT)
unnamed: R44.1, SENS2.2 (VOUT)
unnamed: Q4.1 (G), R36.2, R40.2
unnamed: Q5.1 (G), R37.2, R41.2
unnamed: Q6.1 (G), R38.2, R42.2
unnamed: Q7.1 (G), R39.2, R43.2
PWM_1+: D7.C, R24.2, R25.2, R26.2; also elsewhere on the board
PWM_1-: D7.A, Q4.3 (D); also elsewhere on the board
PWM_2+: D8.C, R27.2, R28.2, R29.2; also elsewhere on the board
PWM_2-: D8.A, Q5.3 (D); also elsewhere on the board
PWM_3+: D9.C, R30.2, R31.2, R32.2; also elsewhere on the board
PWM_3-: D9.A, Q6.3 (D); also elsewhere on the board
PWM_4+: D10.C, R33.2, R34.2, R35.2; also elsewhere on the board
PWM_4-: D10.A, Q7.3 (D); also elsewhere on the board
V_BAT: R26.1, R29.1, R32.1, R35.1; also elsewhere on the board

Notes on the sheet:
PWM and Environment Sensors
30V 3.4A 63 mohm
PWM Outputs
Humidity Sensor
Temperature Sensor
Temperature Sensor 400 mV output at 0 deg C 19.5 mV / deg C slope
Populate one jumper only for each PWM channel. Select from maximum output of 3.3V, 5V, or battery voltage Default configuration is Battery Voltage on Channel 1 (LED Modules), and 5V on Channel 2 (Scaling Lasers)
For Battery outputs, 2.0A maximum current on each PWM channel For +5V outputs, maximum total PWM current is 1.5A For +3.3V outputs, maximum total PWM current is 0.2A

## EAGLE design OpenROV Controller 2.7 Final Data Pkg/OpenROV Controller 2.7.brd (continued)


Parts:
C28, C29, C30: 0.1 uF; R0603
J13: HDR_PINS_2X3
LED3: YELLOW; LED_CHIPLED_0603
Q8, Q9: FDV301N; SOT23
R21: 470; R0603
R46: 1K; R0603
R47: DNP; R0603
R48, R67: 0 (Jumper); R0603
R51, R52, R53, R54, R55, R56, R57, R58: 4.7K; R0603
R62: 10K; R0603
U7: TXB0108SSOP-20; SSOP-20
U8: CAT24C256WI-G; SO8

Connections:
3V3_SCL: Q8.2 (S), R57.1; also elsewhere on the board
3V3_SDA: Q9.2 (S), R58.1; also elsewhere on the board
+3V3: Q8.1 (G), Q9.1 (G), R57.2, R58.2; also elsewhere on the board
+5V: C30.1, J13.2, R55.2, R56.2, U7.19 (VCCB); also elsewhere on the board
BB_3V3: C28.1, C29.1, LED3.A, R46.2, R47.2, R51.2, R52.2, R53.2, R54.2, R62.2, U7.2 (VCCA), U8.8 (VCC); also elsewhere on the board
BB_P9_11: R46.1, U7.8 (A7); also elsewhere on the board
BB_P9_17: U7.4 (A3); also elsewhere on the board
BB_P9_18: U7.6 (A5); also elsewhere on the board
BB_P9_19: R53.1, U8.6 (SCL); also elsewhere on the board
BB_P9_20: R54.1, U8.5 (SDA); also elsewhere on the board
BB_P9_21: U7.7 (A6); also elsewhere on the board
BB_P9_22: U7.5 (A4); also elsewhere on the board
BB_P9_24: R21.2, U7.1 (A1); also elsewhere on the board
BB_P9_26: U7.3 (A2); also elsewhere on the board
BB_SYS_RESET*: R48.2; also elsewhere on the board
D0/UART_RX: U7.20 (B1); also elsewhere on the board
D1/UART_TX: U7.18 (B2); also elsewhere on the board
D20/5V_SDA: Q9.3 (D), R56.1; also elsewhere on the board
D21/5V_SCL: Q8.3 (D), R55.1; also elsewhere on the board
D50/SPI_MISO: J13.1, U7.14 (B6); also elsewhere on the board
D51/SPI_MOSI: J13.4, U7.15 (B5); also elsewhere on the board
D52/SPI_SCK: J13.3, U7.16 (B4); also elsewhere on the board
D53/SPI_SS: U7.17 (B3); also elsewhere on the board
GND: C28.2, C29.2, C30.2, J13.6, R67.1, U7.11 (GND), U8.1 (A0), U8.2 (A1), U8.4 (VSS); also elsewhere on the board
unnamed: R47.1, R48.1, U7.10 (OE)
unnamed: R52.1, R67.2, U8.7 (WP)
unnamed: R51.1, U8.3 (A2)
unnamed: LED3.C, R21.1
unnamed: R62.1, U7.9 (A8)
RESET_N: J13.5, U7.13 (B7); also elsewhere on the board

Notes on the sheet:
I2C and BeagleBone Interface
I2C Interface
5V I2C Bus To Headers
3.3V I2C Bus To Headers
BeagleBone Interface
BeagleBone Cape ID
To DB-25 Connector
ICSP Header
These wires are run on surface traces, that can be cut if it is desired to repurpose the DB-25 pins. This ground pin is tied to the ground plane at the J1 connector, not at the DB-25 connector
Remove resistor for write-protect
BB TX LED


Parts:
C31, C32, C33, C36, C37, C38: 0.1 uF; R0603
C39, C40, C41: 220 uF 35V Low-Impedance; NICHICON_10MM
J14: ESC_PADS-AFRO-12/20A-ESC1; AFRO-ESC-12/20A-ESC1
J15: ESC_PADS-AFRO-12/20A-ESC2; AFRO-ESC-12/20A-ESC2
J16: ESC_PADS-AFRO-12/20A-ESC3; AFRO-ESC-12/20A-ESC3
R49, R50, R66: 10K; R0603
R59, R60, R61: 0.005 1%; R1206
U9, U10, U11: INA199A2; SC70-6L

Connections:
+5V: C31.1, C32.1, C33.1, U9.3 (V+), U10.3 (V+), U11.3 (V+); also elsewhere on the board
ADC1: C38.1, R66.2; also elsewhere on the board
ADC2: C37.1, R50.2; also elsewhere on the board
ADC3: C36.1, R49.2; also elsewhere on the board
ESC1_PWR: C39.+, J14.PWR1, J14.PWR2, R59.2, U9.5 (IN-)
ESC_1A: J14.A1, J14.A2; also elsewhere on the board
ESC_1B: J14.B1, J14.B2; also elsewhere on the board
ESC_1C: J14.C1, J14.C2; also elsewhere on the board
ESC_2A: J15.A1, J15.A2; also elsewhere on the board
ESC_2B: J15.B1, J15.B2; also elsewhere on the board
ESC_2C: J15.C1, J15.C2; also elsewhere on the board
ESC_3A: J16.A1, J16.A2; also elsewhere on the board
ESC_3B: J16.B1, J16.B2; also elsewhere on the board
ESC_3C: J16.C1, J16.C2; also elsewhere on the board
ESC_POWER: R59.1, R60.1, R61.1, U9.4 (IN+), U10.4 (IN+), U11.4 (IN+); also elsewhere on the board
ESC_PWR2: C40.+, J15.PWR1, J15.PWR2, R60.2, U10.5 (IN-)
ESC_PWR3: C41.+, J16.PWR1, J16.PWR2, R61.2, U11.5 (IN-)
GND: C31.2, C32.2, C33.2, C36.2, C37.2, C38.2, C39.-, C40.-, C41.-, J14.GND1, J14.GND2, J15.GND1, J15.GND2, J16.GND1, J16.GND2, U9.1 (REF), U9.2 (GND), U10.1 (REF), U10.2 (GND), U11.1 (REF), U11.2 (GND); also elsewhere on the board
unnamed: R49.1, U9.6 (VOUT)
unnamed: R50.1, U10.6 (VOUT)
unnamed: R66.1, U11.6 (VOUT)

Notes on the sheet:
Motor Current Sensing and ESC Connections
ESC Solder Pads
ESC1
ESC2
ESC3
1206 3/4W or higher
ESC 2 Current 10A Full-Scale Range into 5V A/D
ESC 1 Current 10A Full-Scale Range into 5V A/D
ESC 3 Current 10A Full-Scale Range into 5V A/D



Board: 4 copper layers, 150.0 x 80.0 mm, 191 parts (2 on the bottom side), 159 nets.

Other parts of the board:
U$1: OROV-LOGO-2.00
U$2: CC-LOGO-1

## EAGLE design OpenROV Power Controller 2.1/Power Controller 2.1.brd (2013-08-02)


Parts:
C1, C2, C3, C4, C5, C6, C8, C10: 0.1 uF; C0805K
C7: 4.7 UF; A/3216-18R
C9: 1.0 UF; A/3216-18R
D1, D2, D3, D4: B560; SMC
D5: BZX84B16; TO236
FB1, FB2: HI1206T161R-10; R1206
GND: 1,6/0,9
ISO1: ISO1540; SO8
J1, J4: 22-23-2021
J2: MINI-FIT-JR-18; MINI-FIT-JR-18-PEGS
J3, J7: KK-156-2
J5: 22-23-2071
J6: 22-23-2041
J8, J9, J10: ESC_PADSCUSTOM; ESC-PADS
OC1: 4N33S; DIL6-SMD
Q1: SI4425DDY; SO8
R1, R2: 18K; R0805
R3: 1K; R0805
R4: 6.98K 1%; R0805
R5: 1K 1%; R0805
R6: 10K; R0805
R7, R10, R12: DNP; R0805
R8, R11: 0; R0805
R9, R13: 2.7K; R0805
SCL: 1,6/0,9
SDA: 1,6/0,9
SENSOR_VCC: 1,6/0,9
SPARE: 1,6/0,9
TVS1: SMAJ45CA; DO214AC
U1: ADS7828; SSOP16
U2: LT1129CST-3.3; SOT223
U3: ACS711ELCTR-12AB-T; SOIC127P600X175-8N

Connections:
1A: J2.1, J8.2
1B: J2.2, J8.3
1C: J2.3, J8.4
2A: J2.4, J9.2
2B: J2.5, J9.3
2C: J2.6, J9.4
3A: J2.7, J10.2
3B: J2.8, J10.3
3C: J2.9, J10.4
BATTERY+: D5.C, J2.17, Q1.1 (S), Q1.2 (S), Q1.3 (S), R2.1
GND: C2.2, C3.2, C4.2, C5.2, C6.2, C7.-, C8.2, C9.-, D1.A, D2.A, GND.1, ISO1.5 (GND2), J2.10, J2.18, J3.2, J4.2, J5.1, J7.2, J8.5, J9.5, J10.5, OC1.2 (C), OC1.4 (E), R5.1, R8.1, R11.1, U1.9 (GND), U1.11 (COM), U2.2 (GND), U2.4 (GND), U3.5 (GND)
I2C_SCL: ISO1.6 (SCL2), J2.12, R13.1, SCL.1, U1.14 (SCL)
I2C_SDA: ISO1.7 (SDA2), J2.11, R9.1, SDA.1, U1.15 (SDA)
I2C_VCC: C5.1, C6.1, C7.+, C8.1, ISO1.8 (VCC2), J2.13, R7.2, R9.2, R10.2, R12.1, R13.2, SENSOR_VCC.1, U1.16 (VDD), U2.3 (OUT), U3.8 (VCC)
unnamed: J4.1, OC1.5 (COL), R3.1
unnamed: C10.2, ISO1.4 (GND1), J6.4
unnamed: ISO1.3 (SCL1), J6.3
unnamed: ISO1.2 (SDA1), J6.2
unnamed: C10.1, ISO1.1 (VCC1), J6.1
unnamed: J5.7, U1.3 (CH2)
unnamed: D5.A, Q1.4 (G), R2.2, R3.2
unnamed: C3.1, R6.2, U1.1 (CH0)
unnamed: J5.6, U1.4 (CH3)
unnamed: R7.1, R8.2, U1.13 (A1)
unnamed: R10.1, R11.2, U1.12 (A0)
unnamed: J5.5, U1.5 (CH4)
unnamed: J5.4, U1.6 (CH5)
unnamed: Q1.5 (D), Q1.6 (D), Q1.7 (D), Q1.8 (D), R4.2, U3.1 (IP+), U3.2 (IP+_2)
unnamed: C1.1, D1.C, D3.A, FB1.2, TVS1.C (2)
unnamed: C1.2, D2.C, D4.A, FB2.2, TVS1.A (1)
unnamed: OC1.1 (A), R1.1
unnamed: C2.1, R4.1, R5.2, U1.2 (CH1)
unnamed: J5.3, U1.7 (CH6)
unnamed: J5.2, U1.8 (CH7)
unnamed: C4.1, R12.2, U1.10 (REF)
unnamed: R6.1, U3.7 (VIOUT)
SPARE: J2.14, SPARE.1
TETHER_A: FB1.1, J1.1, J2.16
TETHER_B: FB2.1, J1.2, J2.15
TETHER_POWER: D3.C, D4.C, J3.1, R1.2
V_BAT_SWITCHED: C9.+, J7.1, J8.1, J9.1, J10.1, U2.1 (IN), U3.3 (IP-), U3.4 (IP-_2)

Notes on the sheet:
Homeplug Adapter
BB Cape Power
ESC1
ESC2
ESC3
Tether Power
OpenROV Power Controller 2.1
Molex Connector
I2C Header To Cape
Power Switch
Spare A/D Channels
This work is licensed under the Creative Commons Attribution-NonCommercial-Share Alike 3.0 Unported License. All derivative works are to be attributed to OpenROV.
I2C Address Selection
I2C Pullup Resistors
Sensor I2C


Board: 2 copper layers, 82.9 x 76.2 mm, 52 parts (0 on the bottom side), 41 nets.

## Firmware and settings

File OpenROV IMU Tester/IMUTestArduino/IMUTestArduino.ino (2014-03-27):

// This file is a mix of the MPU9150Lib test code and Walt Homs MS5803 pressure sensor code


////////////////////////////////////////////////////////////////////////////
//
//  This file  part of MPU9150Lib
//
//  Copyright (c) 2013 Pansenti, LLC
//
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
#include <Wire.h>
#include "I2Cdev.h"
#include "MPU9150Lib.h"
#include "CalLib.h"
#include <dmpKey.h>
#include <dmpmap.h>
#include <inv_mpu.h>
#include <inv_mpu_dmp_motion_driver.h>
#include <EEPROM.h>

//  DEVICE_TO_USE selects whether the IMU at address 0x68 (default) or 0x69 is used
//    0 = use the device at 0x68
//    1 = use the device at ox69

//#define  DEVICE_TO_USE    0 // we read a switch to decide which address to use now

MPU9150Lib MPU;                                              // the MPU object

//  MPU_UPDATE_RATE defines the rate (in Hz) at which the MPU updates the sensor data and DMP output

#define MPU_UPDATE_RATE  (20)

//  MAG_UPDATE_RATE defines the rate (in Hz) at which the MPU updates the magnetometer data
//  MAG_UPDATE_RATE should be less than or equal to the MPU_UPDATE_RATE

#define MAG_UPDATE_RATE  (10)

//  MPU_MAG_MIX defines the influence that the magnetometer has on the yaw output.
//  The magnetometer itself is quite noisy so some mixing with the gyro yaw can help
//  significantly. Some example values are defined below:

#define  MPU_MAG_MIX_GYRO_ONLY          0                   // just use gyro yaw
#define  MPU_MAG_MIX_MAG_ONLY           1                   // just use magnetometer and no gyro yaw
#define  MPU_MAG_MIX_GYRO_AND_MAG       10                  // a good mix value 
#define  MPU_MAG_MIX_GYRO_AND_SOME_MAG  50                  // mainly gyros with a bit of mag correction 

//  MPU_LPF_RATE is the low pas filter rate and can be between 5 and 188Hz

#define MPU_LPF_RATE   40

//  SERIAL_PORT_SPEED defines the speed to use for the debug serial port

#define  SERIAL_PORT_SPEED  115200

// pressure sensor //
const int DevAddress = 0x76;  // 7-bit I2C address of the MS5803

// Here are the commands that can be sent to the 5803

const byte Reset = 0x1E;
const byte D1_256 = 0x40;
const byte D1_512 = 0x42;
const byte D1_1024 = 0x44;
const byte D1_2048 = 0x46;
const byte D1_4096 = 0x48;
const byte D2_256 = 0x50;
const byte D2_512 = 0x52;
const byte D2_1024 = 0x54;
const byte D2_2048 = 0x56;
const byte D2_4096 = 0x58;
const byte AdcRead = 0x00;
const byte PromBaseAddress = 0xA0;


unsigned int CalConstant[8];  // Matrix for holding calibration constants

long AdcTemperature, AdcPressure;  // Holds raw ADC data for temperature and pressure
float Temperature, Pressure, TempDifference, Offset, Sensitivity;
float T2, Off2, Sens2;  // Offsets for second-order temperature computation
 
byte ByteHigh, ByteMiddle, ByteLow;  // Variables for I2C reads

#define PIN_LED            13
#define PIN_LED_IMU_OK     6
#define PIN_LED_IMU_FAIL   7
#define PIN_LED_DEPTH_OK   4
#define PIN_LED_DEPTH_FAIL 5

#define PIN_SW_ADDRESS   11
#define PIN_BTN_SOFTRESET 12

boolean boardPresent = false; // is there a board present?
boolean testPass_imu = false; // imu works?
boolean testPass_depth = false; // depth sensor works?
boolean testPass_temp = false; //temperature sensor works?

void setup()
{
  boardPresent = false;
  testPass_imu = false;
  testPass_depth = false;
  testPass_temp = false;
  
  pinMode(PIN_SW_ADDRESS, INPUT);
  digitalWrite(PIN_SW_ADDRESS, HIGH);
  
  pinMode(PIN_BTN_SOFTRESET, INPUT);
  digitalWrite(PIN_BTN_SOFTRESET, HIGH);
  
  pinMode(PIN_LED, OUTPUT);
  pinMode(PIN_LED_IMU_OK, OUTPUT);
  pinMode(PIN_LED_IMU_FAIL, OUTPUT);
  pinMode(PIN_LED_DEPTH_OK, OUTPUT);
  pinMode(PIN_LED_DEPTH_FAIL, OUTPUT);
  
  digitalWrite(PIN_LED, HIGH);
  digitalWrite(PIN_LED_IMU_OK, HIGH);
  digitalWrite(PIN_LED_IMU_FAIL, HIGH);
  digitalWrite(PIN_LED_DEPTH_OK, HIGH);
  digitalWrite(PIN_LED_DEPTH_FAIL, HIGH);
  delay(500);
  digitalWrite(PIN_LED, LOW);
  digitalWrite(PIN_LED_IMU_OK, LOW);
  digitalWrite(PIN_LED_IMU_FAIL, LOW);
  digitalWrite(PIN_LED_DEPTH_OK, LOW);
  digitalWrite(PIN_LED_DEPTH_FAIL, LOW);
  
  Serial.begin(SERIAL_PORT_SPEED);
    Serial.println("Program start");
    
    /*
    while(!Serial.available())
    {
      Serial.println("Press any key to continue");
      delay(500);
    }*/
  
  Wire.begin();
  sendCommand(Reset);
  delay(10);
  delay(1000);
  Serial.println("Device is reset");
   
  // Get the calibration constants and store in array (for pressure sensor)

  
  for (byte i = 0; i < 8; i++)
  {
    sendCommand(PromBaseAddress + (2*i));
    Wire.requestFrom(DevAddress, 2);
    while(Wire.available()){
      ByteHigh = Wire.read();
      ByteLow = Wire.read();
    }
    CalConstant[i] = (((unsigned int)ByteHigh << 8) + ByteLow);
  }

}

void loop2() // test loop to swap with main loop for quick trials
{
  Serial.println("Test");
  digitalWrite(PIN_LED_IMU_OK, digitalRead(PIN_BTN_SOFTRESET));
}

void loop()
{  
  boolean addrSwitchPos = digitalRead(PIN_SW_ADDRESS); // keep track so we can reset if this is changed after testing  
  float pressure = 0, temp = 0;

  // test IMU
  MPU.selectDevice(addrSwitchPos);                         // only needed if device has changed since init but good form anyway
  if(MPU.init(MPU_UPDATE_RATE, MPU_MAG_MIX_GYRO_AND_MAG, MAG_UPDATE_RATE, MPU_LPF_RATE))   // start the MPU
    testPass_imu = true; // pass if we can initialize, just show we are talking to the imu
  
  // test pressure
  pressure = getPressure();
  if((pressure<1) && (pressure > -1))
      testPass_depth = true;
  
  // test temperature
  temp = getTemp();
  if(temp > 0)
    if(temp < 100)
      if(temp != 20) // this seems to be the value with no sensor connected
        testPass_temp = true;
  Serial.print("Temp: ");
  Serial.println(temp);
  
  // results
  Serial.println("--------------------------------");
  Serial.println("Test results");
  Serial.print("IMU  : ");
  if(testPass_imu)
  {
    digitalWrite(PIN_LED_IMU_OK, HIGH);    
    Serial.println("PASS");
  }
  else
  {
    digitalWrite(PIN_LED_IMU_FAIL, HIGH);    
    Serial.println("FAIL");
  }
  Serial.print("DEPTH: ");
  if(testPass_depth)
  {
    digitalWrite(PIN_LED_DEPTH_OK, HIGH);
    Serial.println("PASS");
  }
  else
  {    
    digitalWrite(PIN_LED_DEPTH_FAIL, HIGH);
    Serial.println("FAIL");  
  }
  Serial.print("TEMP : ");
  if(testPass_temp)
    Serial.println("PASS");
  else
    Serial.println("FAIL");
  
  Serial.println("--------------------------------");
  // tests complete
  
    
  // get stuck until a new board is inserted
  Serial.println("Test complete, press any key to retest or use hardware soft reset button.");
  while(true)
  {
    
    if(Serial.available()) break;
    if(!digitalRead(PIN_BTN_SOFTRESET)) break;
    if(digitalRead(PIN_SW_ADDRESS) != addrSwitchPos) break;
    if(testPass_imu && testPass_temp && testPass_depth)
    {
      digitalWrite(PIN_LED, HIGH);
      delay(100);
    }
    else
    {
    digitalWrite(PIN_LED, HIGH);
      delay(250);
      digitalWrite(PIN_LED, LOW);
      delay(250);
    }

  }
  
  setup();
  
}

float getPressure()
{
  sendCommand(D1_512);
  delay(10);
  sendCommand(AdcRead);
  Wire.requestFrom(DevAddress, 3);
  while(Wire.available())
  {
    ByteHigh = Wire.read();
    ByteMiddle = Wire.read();
    ByteLow = Wire.read();
  }
  AdcPressure = ((long)ByteHigh << 16) + ((long)ByteMiddle << 8) + (long)ByteLow;
  
  // Calculate the pressure parameters
  
  Offset = (float)CalConstant[2] * pow(2,16);
  Offset = Offset + ((float)CalConstant[4] * TempDifference / pow(2, 7));

  Sensitivity = (float)CalConstant[1] * pow(2, 15);
  Sensitivity = Sensitivity + ((float)CalConstant[3] * TempDifference / pow(2, 8));
  
  // Add second-order corrections
  
  Offset = Offset - Off2;
  Sensitivity = Sensitivity - Sens2;
  
  // Calculate absolute pressure in bars

  Pressure = (float)AdcPressure * Sensitivity / pow(2, 21);
  Pressure = Pressure - Offset;
  Pressure = Pressure / pow(2, 15);
  Pressure = Pressure / 10000;  // Set output to bars;
  
  // Convert to psig and display
  
  Pressure = Pressure - 1.015;  // Convert to gauge pressure (subtract atmospheric pressure)
  Pressure = Pressure * 14.50377;  // Convert bars to psi
  Serial.print("Pressure in psi is: ");
  Serial.println(Pressure);
  Serial.println();
  
  return Pressure;
}

float getTemp()
{
  sendCommand(D2_512);
  delay(10);
  sendCommand(AdcRead);
  Wire.requestFrom(DevAddress, 3);
  while(Wire.available())
  {
    ByteHigh = Wire.read();
    ByteMiddle = Wire.read();
    ByteLow = Wire.read();
  }
  AdcTemperature = ((long)ByteHigh << 16) + ((long)ByteMiddle << 8) + (long)ByteLow;
 // Serial.print("D2 is: ");
//  Serial.println(AdcTemperature);
  
    
  // Calculate the Temperature (first-order computation)
  
  TempDifference = (float)(AdcTemperature - ((long)CalConstant[5] << 8));
  Temperature = (TempDifference * (float)CalConstant[6])/ pow(2, 23);
  Temperature = Temperature + 2000;  // This is the temperature in hundredths of a degree C
  
  // Calculate the second-order offsets
  
  if (Temperature < 2000.0)  // Is temperature below or above 20.00 deg C ?
  {
    T2 = 3 * pow(TempDifference, 2) / pow(2, 33);
    Off2 = 1.5 * pow((Temperature - 2000.0), 2);
    Sens2 = 0.625 * pow((Temperature - 2000.0), 2);
  }
  else
  {
    T2 = (TempDifference * TempDifference) * 7 / pow(2, 37);
    Off2 = 0.0625 * pow((Temperature - 2000.0), 2); 
    Sens2 = 0.0;
  }
  
  // Check print the offsets
  
  Serial.println("Second-order offsets are:");
  Serial.println(T2);
  Serial.println(Off2);
  Serial.println(Sens2);
  
  
  // Print the temperature results
  
  Temperature = Temperature / 100;  // Convert to degrees C
  Serial.print("First-Order Temperature in Degrees C is ");
  Serial.println(Temperature);
  Serial.print("Second-Order Temperature in Degrees C is ");
  Serial.println(Temperature - (T2 / 100));
  
  return Temperature;
}

void sendCommand(byte command){
  Wire.beginTransmission(DevAddress);
  Wire.write(command);
  Wire.endTransmission();
}

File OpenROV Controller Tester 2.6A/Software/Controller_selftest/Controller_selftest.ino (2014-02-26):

/* Self-Test Code for OpenROV Controller Board 2.5

Initial Version 6 September 2013 W. Holm

*/

#include <Wire.h>

/* The following declarations are used for the I2C A/D converter on the test jig

     A/D Channels are as follows:
     Ch0 = 5V power
     Ch1 = 3.3V power
     Ch2 = Battery voltage, probed at PWM1+ pin
     
*/

const byte voltage5V = 1;
const byte voltage3V = 0;
const byte voltageBat = 2;

const int I2C_address = 0x48;  // I2C write address for A/D converter
const byte DAT[8] = {0x8C,0xCC,0x9C,0xDC,0xAC,0xEC,0xBC,0xFC};
                                 // Constant configuration data for A/D converter input mux
  

int adcOutput;    // temp used to hold 12-bit unsigned output of I2C A/D or 10-bit Mega A/D

/*  The following constants set the thresholds for the analog voltage checks on the I2C A/D converter
  The full-scale range is 0-4095 counts, corresponding to 0-2.5V
  The battery voltage (12.0V on test jig) is sensed through a 1:5 resistor divider.  Battery voltage should be
      2.0V +/-5%
  The 5V supply is sensed through a 1:2 resistor divider.  5V supply should be 1.666V +/- 5%
  3.3V supply is sensed through a 1:1 resistor divider.  3.3V supply should be 1.65V +/- 5%
*/

const int voltage5V_High = 2867;
const int voltage5V_Low = 2593;
const int voltage3V_High = 2838;
const int voltage3V_Low = 2568;
const int voltageBat_High = 3440;
const int voltageBat_Low = 3112;

/* The following constants set the thresholds for the analog current and voltage checks with the Mega A/D converter
  The full-scale range of the Mega A/D converter is 0-1023 counts, corresponding to 0-(the 5V supply voltage).
  The measured current draw on board 2.5A #001 has been between 6 and 20 counts.  For now, tolerance band on board current is 3-25.
*/

const int currentBoard_High = 25;
const int currentBoard_Low = 3;
//const int currentBat_High = xxx;
//const int currentBat_Low = xxx;
const int voltageMegaBat_High = 675;
const int voltageMegaBat_Low = 552;

void setup()
{
  Wire.begin();    // initialize Arduino Mega I2C port
  
  pinMode(13, OUTPUT);         // D13 LED
  pinMode(49, OUTPUT);          // D49 LED
  pinMode(1, OUTPUT);       // BB UART RX LED
  
  
}

void loop()
{
  
  /* Flash the LEDs for 1 second.  HIGH = LED on for 13 and 49, LOW for LED1 */
  digitalWrite(13, HIGH);
  digitalWrite(49, HIGH);
  digitalWrite(1, LOW); 
  delay(1000);
  digitalWrite(13, LOW);
  digitalWrite(49, LOW);
  digitalWrite(1, HIGH);
  delay(1000);
  
  /* Do a couple of dummy reads to clear the A/D */
  
  adcOutput = readADC(voltageBat);
  adcOutput = readADC(voltageBat);
  adcOutput = readADC(voltageBat); 
  
  /* Read the 12V test jig supply on the I2C A/D */

  adcOutput = readADC(voltageBat);
  if (adcOutput > voltageBat_High) blinkError(2); 
  if (adcOutput < voltageBat_Low) blinkError(2);

  /* Read the 5V supply on the I2C A/D */
  adcOutput = readADC(voltage5V);
  if (adcOutput > voltage5V_High) blinkError(3);
  if (adcOutput < voltage5V_Low) blinkError(3);

  /* Read the 3.3V supply on the I2C A/D */
  adcOutput = readADC(voltage3V);
  if (adcOutput > voltage3V_High) blinkError(4);
  if (adcOutput < voltage3V_Low) blinkError(4);

  /* Read the board current on the Mega A/D  */

  adcOutput = analogRead(0);
  if (adcOutput > currentBoard_High) blinkError(4);
  if (adcOutput < currentBoard_Low) blinkError(4);


  /* Read Battery1 current on the Mega A/D  */
 
  /* as a test, output the battery current to serial port #1 (D18) */
  Serial1.begin(9600);

  adcOutput = analogRead(6);
  Serial1.println(adcOutput);

  adcOutput = analogRead(6);
  Serial1.println(adcOutput);

  adcOutput = analogRead(6);
  Serial1.println(adcOutput);

  adcOutput = analogRead(6);
  Serial1.println(adcOutput);

  adcOutput = analogRead(6);
  Serial1.println(adcOutput);
 
 
 adcOutput = analogRead(6);
 
  /* Read Battery2 current on the Mega A/D  */

 adcOutput = analogRead(5);
 
  /*  Read battery voltage on the Mega A/D */

 adcOutput = analogRead(4);
 if (adcOutput > voltageMegaBat_High) blinkError(8);
 if (adcOutput < voltageMegaBat_Low) blinkError(8);
 
  /* Turn on PWM channels 1 (digital 44) and 2 (digital 45) and declare success */

  analogWrite(44, 128);
  analogWrite(45, 128);
  blinkSuccess();

}

 /* Read the desired channel from the A/D converter.  If the A/D converter does not respond, go to blink error #1 */
  
int readADC( byte channel)  // This function reads the appropriate channel of the A/D and returns the 12-bit value
{
  byte adval_High, adval_Low;    // Store A/D value (high byte, low byte)
  int adval;

  Wire.beginTransmission(I2C_address);
  Wire.write(DAT[channel]);        // Configure the device to read the called channel  
  Wire.endTransmission(); 
  delay(1);
    
  // Read A/D value
  Wire.requestFrom(I2C_address, 2);
  delay(100);
  if(Wire.available() == 2)          // Checkf for data from A/D converter
  { 
    adval_High = Wire.read();   // Receive A/D high byte
    adval_Low = Wire.read();    // Receive A/D low byte
    adval = (adval_High << 8) | adval_Low;
    return(adval);
  }
  else blinkError(1);
  return (-1);
  
}
  

void blinkSuccess()  // alternate LEDs 13 and 49 at 1 Hz overall rate
{
  while(1)
  {
    digitalWrite(13, LOW);
    digitalWrite(49, HIGH);
    delay(500); 
    digitalWrite(13, HIGH);
    digitalWrite(49, LOW);
    delay(500);
  }
}

void blinkError(int errNo)  // hold LED13 on, blink LED 49 to represent error number
{
  int count;
  digitalWrite(13, HIGH);
  while(1)
  {
    count = errNo;
    while(count > 0)
    {
      digitalWrite(49, HIGH);
      delay(250);
      digitalWrite(49, LOW);
      delay(250);
      count = count-1;
    }
    delay(1000);
  }
}

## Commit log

2012-06-04 Added Eagle sch file for OpenROV BeagleBone Cape
    [OpenROV Cape.sch]
2012-06-09 updated with correct BB RX resistor placement
    [OpenROV-mcu.fzz]
2012-06-09 changed voltage divider for arduino to work
    [OpenROV Cape.sch]
2012-06-09 started on new cape board
    [Open_ROV_Cape.brd, Open_ROV_Cape.sch]
2012-06-11 start of PCB layout based on the adafruit cape
    [OpenROV Cape.brd, OpenROV Cape.sch]
2012-06-12 removed the extra beagle board header pins to make more room for arduino pins
    [OpenROV Cape.brd, OpenROV Cape.sch]
2012-06-12 swapped out IC1 for official sparkfun atmega328 footprint
    [OpenROV Cape.brd, OpenROV Cape.sch]
2012-06-12 swapped out the giant crystal footprint for a smaller standard one with the same hole spacing
    [OpenROV Cape.brd, OpenROV Cape.sch]
2012-06-12 moved servo headers back over to the right side of the board
    [OpenROV Cape.brd]
2012-06-12 added headers for +9V and +12V
    [OpenROV Cape.brd, OpenROV Cape.sch]
2012-07-10 OpenROV Cape with features for first proto build
    Added
    *Arduino headers for shield
    *Lights for Power, UART Tx/Rx, and pin 13
    *Header for FTDI programmer
    *Power FETs for higher power PWM output
    *Header for tilt servo
    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
2012-07-24 Added values and fixed errors
    Added/ corrected values to most components, corrected erroneous voltage
    divider configuration to TX-O, added resister between BBTX and RX-I,
    changed sheet labels
    [OpenROV Cape.brd, OpenROV Cape.sch]
2012-07-26 Disambiguated several features
    [OpenROV Cape.brd, OpenROV Cape.sch]
2012-12-03 Removing old schematics and adding the new cape, both PDF design schematics and gerber files
    [BeagleBone OpenROV Cape Rev A1.xls, OpenROV Cape.brd, OpenROV Cape.sch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]
2013-01-04 Added wiring schematics, based on current cape design
    Wiring schematics, based on current cape design.
    Drawn in CADInt (www.cadint.se)
2013-08-02 added Power Control Board 2.1 schematics, gerbers and PDFs
    [Power Controller 2.1.brd, Power Controller 2.1.sch, PowerBoard 2.1 BOM.xls]
2013-09-27 added OpenROV Controller v2.5B files, gerbers, schematics. Reorganized folders
    [BeagleBone OpenROV Cape Rev A1.xls, OpenROV Controller 2.5B BOM Rev1.xls, OpenROV Controller 2.5B.brd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]
2014-01-30 Added first version of Controller Tester that went out to manufacturing
    [Ctrl2.6Tester.kicad_pcb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]
2014-02-01 Added Controller 2.6 files and Topside Adapter Board 2.6 files
    [OpenROV Controller 2.6 BOM.xls, OpenROV Controller 2.6.brd, OpenROV Controller 2.6.sch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]
2014-02-20 added image of test jig setup and software needed to test control boards
2014-03-27 added IMU tester board pictures, software, and text file with info.
    [IMUTesterBottom.dxf]
2014-12-17 Added 2.7 Controllerboard and the light board
    [OpenROV Controller 2.7 BOM.xls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]
2015-09-18 Added 2.8 Files
    2.8 Control Board Final Data Package, 2.8 Light Board Final Data Package
    [OpenROV Controller 2.7 BOM.xls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]
2015-09-23 Added IMU/Depth Module v2
    Data Package for IMU/Depth Module v2
    [BNO055+MS5838BoB.v02 BOM.xls, BNO055+MS5838BoB.v02.brd, BNO055+MS5838BoB.v02.sch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]
2015-11-24 Added Light Board 2.8A Data Package
    [OpenROV Light Board 2.8A.GBL, OpenROV Light Board 2.8A.GBO, OpenROV Light Board 2.8A.GBS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]
2015-11-24 Added External Light Cube Package
    [Light Cube BOM.xls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]
2015-12-09 BOM Rev 1 added
    Changed the LED to a more efficient one.
    [Light Cube BOM Rev1.xls, Light Cube BOM.xls]
2016-03-16 Added 2.6A Data Package
    [OpenROV Topside Interface 2.6A BOM.xls, OpenROV Topside Interface 2.6A.brd, OpenROV Topside Interface 2.6A.sch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]

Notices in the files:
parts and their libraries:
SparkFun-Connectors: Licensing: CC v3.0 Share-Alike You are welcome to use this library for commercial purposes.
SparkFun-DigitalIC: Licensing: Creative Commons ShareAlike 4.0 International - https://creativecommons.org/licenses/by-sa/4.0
